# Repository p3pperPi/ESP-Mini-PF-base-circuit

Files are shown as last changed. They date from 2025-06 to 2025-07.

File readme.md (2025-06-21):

# 概要
ESP32を使用して、DCブラシモータを使用したライントレースをするための基板です。

# 回路図

回路図

# 機能
## 電源
J1の PHコネクタ、もしくは J3の XT60コネクタに電源を接続してください。
J1の PHコネクタを使用する際は、J2の PHコネクタにスイッチをつないでください。

入力可能な電圧の範囲はは ** 30V** です。

また、JP17をショートすることで、モータ電源にUSB 5Vを使用することが可能です。
ただし、JP17をショートした状態で電源コネクタに5V以外の電圧をかけると、接続した機器が破損します。
**JP17をショートさせた際は、絶対に電源コネクタから給電は行わないでください。**
なお、JP17にはダイオードを入れて逆流防止を行うことも可能です。その際は、[SBM245L](https://akizukidenshi.com/catalog/g/g117439/)を使用してください。

入力電源は、DCDCコンバータモジュール[CN39033A](https://japanese.alibaba.com/product-detail/CN3903-3A-Mini-Buck-Step-Down-1600380707339.html)を使用して5Vまで電圧を下げられます。

| 項目 | 値  | 単位 |
| --- | --- | ---- |
| 最大定格入力電圧 | 30  | V |
| 出力電流(Max.) | 3 | A |

上で生成された5Vから、[UZ1085L-22-TN3-R](https://www.lcsc.com/product-detail/Low-Dropout-Regulators-LDO_UZ1085L-AD-TN3-R_C146666.html)を使用し、マイコンへの電源供給を行います。
| 項目 | 値  | 単位 |
| --- | --- | ---- |
| 最大定格入力電圧 | 18  | V |
| 最大電流(Typ.) | 4 | A |

## マイコン
ESP32-WROOM-32を使用します。  
[CH340X](https://www.lcsc.com/product-detail/USB-Converters_WCH-Jiangsu-Qin-Heng-CH340X_C3035748.html?s_z=n_CH340X)を使用した書き込み回路を持ちます。

## DCブラシモータ
モータドライバIC[CP3119MDTR](https://www.lcsc.com/product-detail/Brushed-DC-Motor-Drivers_XBLW-CP3119MDTR-XBLW_C42395499.html)を使用して、DCモータを制御します。

| 項目 | 値 | 単位 |
| --- | --- | --- |
| 最大定格電圧 | 32 | V |
| 最大定格電流 | 8.0 | A |
| 推奨電源電圧範囲 | 3.0~30.0 | V |
| 推奨最大電流 | 6.0 | A |
| FETオン抵抗 (load=1A) | 80 | m $\Omega$ |
| FETオン抵抗 (load=3A) | 110 | m $\Omega$ |

## エンコーダ
A/B相のシングルエンドエンコーダをカウントします。エンコーダの電源電圧と信号入力は5Vです。
[TXB0104RUT](https://lcsc.com/product-detail/translators-level-shifters_texas-instruments-txb0104rutr_C105266.html)により、5V信号を3.3Vに変換してESP32に信号を入力します。
パルス入力ピンは、ソルダジャンパ(JP2 ~ 5)によりプルアップが可能です。
プルアップの有無については、[ジャンパの機能](#ジャンパの機能)を参照してください。

## 汎用IO
サーボモータ、センサ入力等のための、汎用のIOです。
ピンアサインは下記の通りです。

| ピン | 機能 |
| ---- | --- |
| 1 | IOピン |
| 2 | Vs |
| 3 | GND |

ピン番号は、[ピンアサイン](#ピンアサイン)を参照してください。

Vsは、ソルダジャンパ(JP6 ~ 9)により電圧を選択可能です。
選択される電圧は、[ジャンパの機能](#ジャンパの機能)を参照してください。

## フォトリフレクタ
[ITR8307/S17/TR8(B)](https://www.lcsc.com/product-detail/Reflective-Optical-Interrupters_Everlight-Elec-ITR8307-S17-TR8-B_C81632.html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) を3つ搭載し、テープの判定を行います。

また、外付けのLED・フォトトランジスタを使用することも可能です。いずれも外形3mmの砲弾型のものを使用してください。

使用するフォトリフレクタの選択は、JP10～JP15 を使用してください。

## LED
3mm砲弾型LEDを4つ搭載可能です。  
D2は、電源投入時に点灯します。  
D3, D4, D5はESP32から点灯/消灯 を管理可能です。

# ピンアサイン

ESP32-WROOM-32のピンアサインは下記の通りです。

| ピン | IO pin | 機能 | IN/OUT |
| ---- | --- | --- | --- |
| 27 | IO16 | モータL出力1 | OUT (PWM) |
| 28 | IO17 | モータL出力2 | OUT (PWM) |
| 30 | IO18 | モータR出力1 | OUT (PWM) |
| 31 | IO19 | モータR出力2 | OUT (PWM) |
| 16 | IO13 | エンコーダL入力1 | IN (PWM) |
| 13 | IO14 | エンコーダL入力2 | IN (PWM) |
| 10 | IO25 | エンコーダR入力1 | IN (PWM) |
| 11 | IO26 | エンコーダR入力2 | IN (PWM) |
| 34 | IO3/RxD0 | PCとのUART RxD | IN (COM.) |
| 35 | IO1/TxD0 | PCとのUART TxD | OUT (COM.) |
| 25 | IO0 | Boot | - |
| 9 | IO33 | ラインセンサ1 | IN(Analog) |
| 6 | IO34 | ラインセンサ2 | IN(Analog) |
| 8 | IO35 | ラインセンサ3 | IN(Analog) |
| 33 | IO21 | LED 赤 | OUT(Digital) |
| 36 | IO22 | LED 黄 | OUT(Digital) |
| 37 | IO23 | LED 緑 | OUT(Digital) |
| 8 | IO32 | 汎用IO 0 | IN/OUT |
| 12 | IO27 | 汎用IO 1 | IN/OUT |
| 26 | IO4 | 汎用IO 2 | IN/OUT |
| 29 | IO5 | 汎用IO 3(プルアップ) | IN/OUT |
| 4 | IO36(SENSOR_VP) | 電源電圧監視(1/10) | IN(Analog) |

# ジャンパの機能

ジャンパにより、機能を切り替えることができます。

| ジャンパ | 機能 | モード1  | 機能1 | モード2  | 機能2 | デフォルト | 備考 |
| --- | --- | --- | --- | --- | --- | --- | --- |
| JP1 | Power_SW_Disable | オープン | J2 パワースイッチが有効 | ショート | J2 パワースイッチが無効(常時ショート) | オープン | - |
| JP2 | L1_PU | オープン | エンコーダL1の入力は電圧入力 | ショート | エンコーダL1の入力をプルアップ(1k) | オープン | - |
| JP3 | L2_PU | オープン | エンコーダL2の入力は電圧入力 | ショート | エンコーダL2の入力をプルアップ(1k) | オープン | - |
| JP4 | R1_PU | オープン | エンコーダR1の入力は電圧入力 | ショート | エンコーダR1の入力をプルアップ(1k) | オープン | - |
| JP5 | R2_PU | オープン | エンコーダR2の入力は電圧入力 | ショート | エンコーダR2の入力をプルアップ(1k) | オープン | - |
| JP6 | Vs_SEL0 | 3.3 | 汎用入力J9 の2番ピンを3.3Vにする | Vin | 汎用入力J9 の2番ピンをVinにする | オープン | オープンだと2番ピンはNC |
| JP7 | Vs_SEL1 | 3.3 | 汎用入力J10 の2番ピンを3.3Vにする | Vin | 汎用入力J10 の2番ピンをVinにする | オープン | オープンだと2番ピンはNC |
| JP8 | Vs_SEL2 | 3.3 | 汎用入力J11 の2番ピンを3.3Vにする | Vin | 汎用入力J11 の2番ピンをVinにする | オープン | オープンだと2番ピンはNC |
| JP9 | Vs_SEL3 | 3.3 | 汎用入力J12 の2番ピンを3.3Vにする | Vin | 汎用入力J12 の2番ピンをVinにする | オープン | オープンだと2番ピンはNC |
| JP10 | LED_SEL1 | SMD | ラインセンサ(U8)の LEDを有効化 | DIP | D6 のLEDを有効化 | オープン | オープンだとU8, D6いずれのLEDも光らない  |
| JP11 | PT_SEL1 | SMD | SENSOR1 の入力をラインセンサU8 にする  | DIP | SENSOR1 の入力をQ1 にする | オープン | オープンだとSENSOR1 はN.C. |
| JP12 | LED_SEL2 | SMD | ラインセンサ(U9)の LEDを有効化 | DIP | D7 のLEDを有効化 | オープン | オープンだとU9, D7いずれのLEDも光らない  |
| JP13 | PT_SEL2 | SMD | SENSOR2 の入力をラインセンサU9 にする  | DIP | SENSOR2 の入力をQ2 にする | オープン | オープンだとSENSOR2 はN.C. |
| JP14 | LED_SEL2 | SMD | ラインセンサ(U10)の LEDを有効化 | DIP | D8 のLEDを有効化 | オープン | オープンだとU10, D8いずれのLEDも光らない |
| JP15 | PT_SEL2 | SMD | SENSOR3 の入力をラインセンサU10 にする | DIP | SENSOR3 の入力をQ1 にする | オープン | オープンだとSENSOR3 はN.C. |
| JP16 | Reseet | オープン | 通常動作 | ショート | リセット | オープン | スイッチ取付可 |
| JP17 | USB＿Vs | オープン | 外部電源をモータ電源とする | ショート | USB電源をモータ電源とする | オープン | ショートの代わりにダイオードを使用可 |

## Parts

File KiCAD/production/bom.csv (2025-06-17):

Designator | Footprint | Quantity | Value | LCSC Part #
C1, C2 | CP_Radial_D5.0mm_P2.00mm | 2 | 22u | x
C10, C3, C4, C8 | 0402 | 4 | 0.1u | C77020
C5 | 0402 | 1 | 10u | C76991
C6 | 0402 | 1 | 20p | C76959
C7, C9 | CP_Radial_D8.0mm_P3.50mm | 2 | 470u | x
D1 | D_SMA | 1 | CDBA240LL-HF | C2886093
D2 | LED_D3.0mm | 1 | LED_POWER | x
D3 | LED_D3.0mm | 1 | LED_R | x
D4 | LED_D3.0mm | 1 | LED_Y | x
D5 | LED_D3.0mm | 1 | LED_G | x
D6, D7, D8 | LED_D3.0mm | 3 | U4_ALT1 | x
F1 | 0603 | 1 | BSMD0603-050-6V | C883095
J1 | JST_PH_B2B-PH-K_1x02_P2.00mm_Vertical | 1 | Vin_1 | x
J10 | PinHeader_1x03_P2.54mm_Vertical | 1 | IO27_GPIO1 | x
J11 | PinHeader_1x03_P2.54mm_Vertical | 1 | IO32_GPIO2 | x
J12 | PinHeader_1x03_P2.54mm_Vertical | 1 | IO5_GPIO3(PU) | x
J2 | JST_PH_B2B-PH-K_1x02_P2.00mm_Vertical | 1 | Power_SW | x
J3 | AMASS_XT60-M_1x02_P7.20mm_Vertical | 1 | Vin_XT | x
J4 | USB_Micro-B_Amphenol_10103594-0001LF_Horizontal | 1 | USB_B_Micro | C428495
J5 | JST_ZH_B4B-ZH-A_1x04_P1.50mm_Vertical | 1 | Encorder_L | x
J6 | JST_ZH_B4B-ZH-A_1x04_P1.50mm_Vertical | 1 | Encorder_R | x
J7 | TerminalBlock_bornier-2_P5.08mm | 1 | MOTOR_L | x
J8 | TerminalBlock_bornier-2_P5.08mm | 1 | MOTOR_R | x
J9 | PinHeader_1x03_P2.54mm_Vertical | 1 | IO4_GPIO0 | x
JP1 | SolderJumper-2_P1.3mm_Open_RoundedPad1.0x1.5mm | 1 | Power_SW_DIisable | x
JP10, JP12, JP14 | SolderJumper-3_P1.3mm_Open_RoundedPad1.0x1.5mm | 3 | LED_SEL1 | x
JP11, JP13, JP15 | SolderJumper-3_P1.3mm_Open_RoundedPad1.0x1.5mm | 3 | PT_SEL1 | x
JP16 | SolderJumper-2_TVAF06-A020B-R_COMPATIBLE | 1 | Reset | x
JP17 | D_DO-41_SOD81_P7.62mm_Horizontal | 1 | USB_Vs | x
JP2 | SolderJumper-2_P1.3mm_Open_RoundedPad1.0x1.5mm | 1 | L1_PU | x
JP3 | SolderJumper-2_P1.3mm_Open_RoundedPad1.0x1.5mm | 1 | L2_PU | x
JP4 | SolderJumper-2_P1.3mm_Open_RoundedPad1.0x1.5mm | 1 | R1_PU | x
JP5 | SolderJumper-2_P1.3mm_Open_RoundedPad1.0x1.5mm | 1 | R2_PU | x
JP6 | SolderJumper-3_P1.3mm_Open_RoundedPad1.0x1.5mm | 1 | Vs_SEL0 | x
JP7 | SolderJumper-3_P1.3mm_Open_RoundedPad1.0x1.5mm | 1 | Vs_SEL1 | x
JP8 | SolderJumper-3_P1.3mm_Open_RoundedPad1.0x1.5mm | 1 | Vs_SEL2 | x
JP9 | SolderJumper-3_P1.3mm_Open_RoundedPad1.0x1.5mm | 1 | Vs_SEL3 | x
Q1, Q2, Q3 | LED_D3.0mm | 3 | U4_ALT2 | x
R1 | 0402 | 1 | 18k | C316875
R10, R11, R12, R13, R17, R18, R19, R20, R22, R24, R26, R6, R8 | 0402 | 13 | 1k | C159872
R14, R15, R16, R7, R9 | 0402 | 5 | 560 | C427239
R2 | 0402 | 1 | 2k | C173345
R21, R23, R25 | 0805 | 3 | 50 | C2828866
R3, R4 | 0402 | 2 | 22 | C400511
R5 | 0402 | 1 | 4.7k | C159885
U1 | DCDC_Conv_CN39033A | 1 | CN39033A | x
U10, U8, U9 | Everlight_ITR1201SR10AR | 3 | ITR8307-S17-TR8 | C81632
U2 | MSOP-10_3x3mm_P0.5mm | 1 | CH340X | C3035748
U3 | TO-252-2 | 1 | UZ1085L-33-TN3-R | C125622
U4 | Texas_R-PUQFN-N12 | 1 | TXB0104RUT | C105266
U5, U6 | SOP-8_3.9x4.9mm_P1.27mm | 2 | CP3119MDTR | C42395499
U7 | ESP32-WROOM-32_39P-TH | 1 | ESP32-WROOM-32 | x

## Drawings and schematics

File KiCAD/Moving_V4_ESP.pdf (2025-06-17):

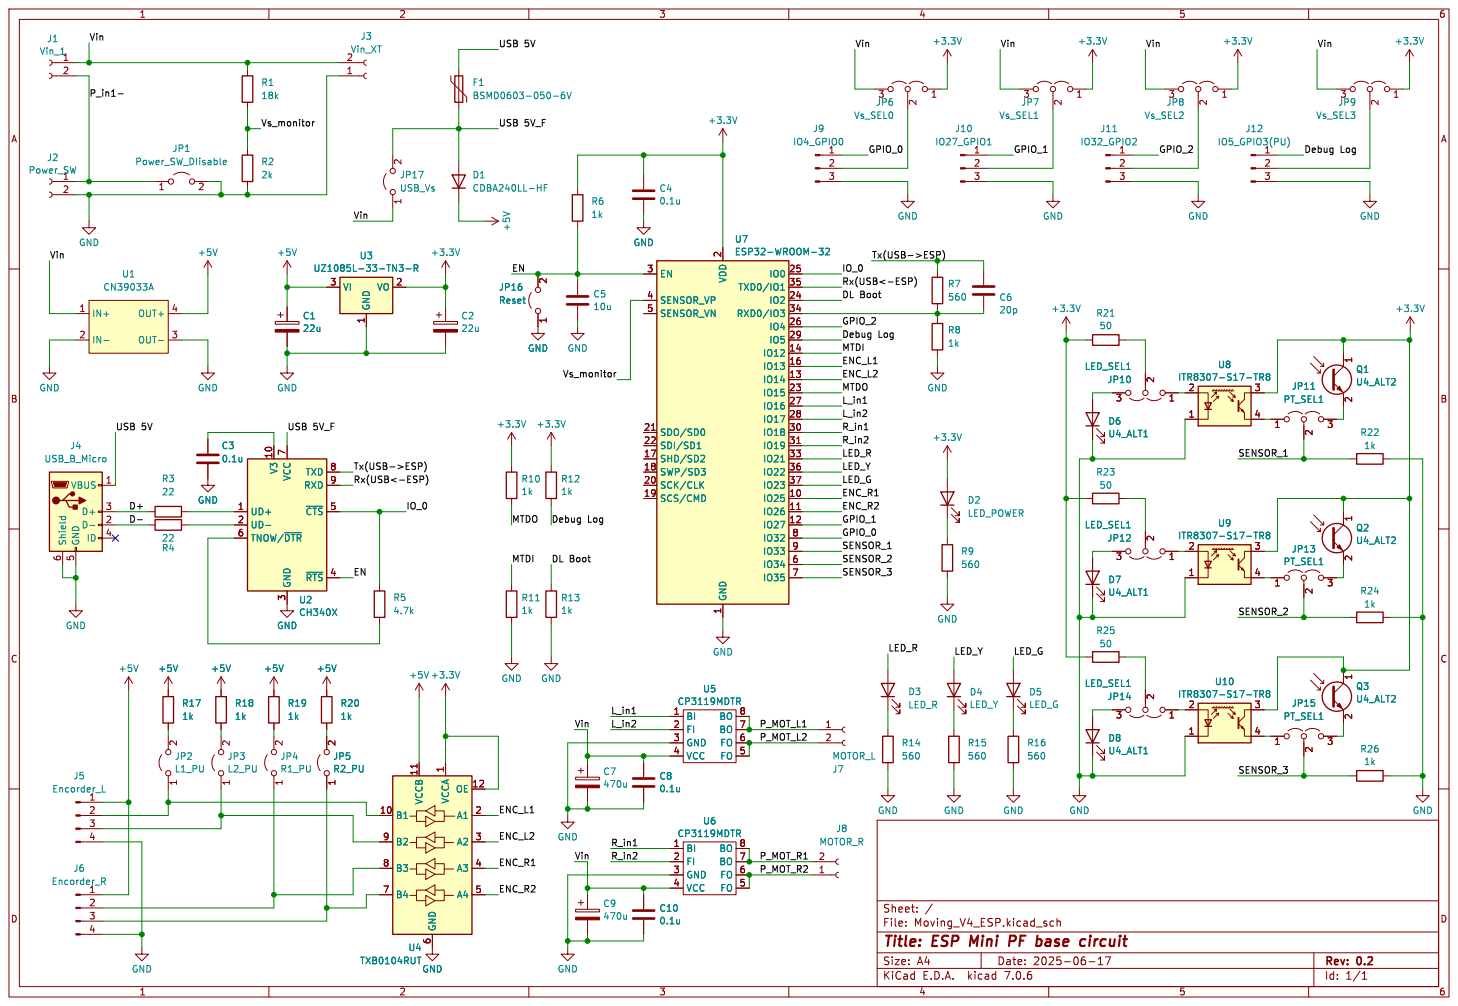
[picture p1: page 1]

2 SCK/CLK 20 SDO/SD0 21 SDI/SD1 22

7 TXD 8 RXD 9 U2 CH340X GND GND

3 ~{RTS}4 ~{CTS}5 TNOW/~{DTR} 6 VCC

Tx(USB->ESP) EN
IO_0 Rx(USB<-ESP)

Id: 1/1 Title: ESP Mini PF base circuit File: Moving_V4_ESP.kicad_sch Sheet: / +5V

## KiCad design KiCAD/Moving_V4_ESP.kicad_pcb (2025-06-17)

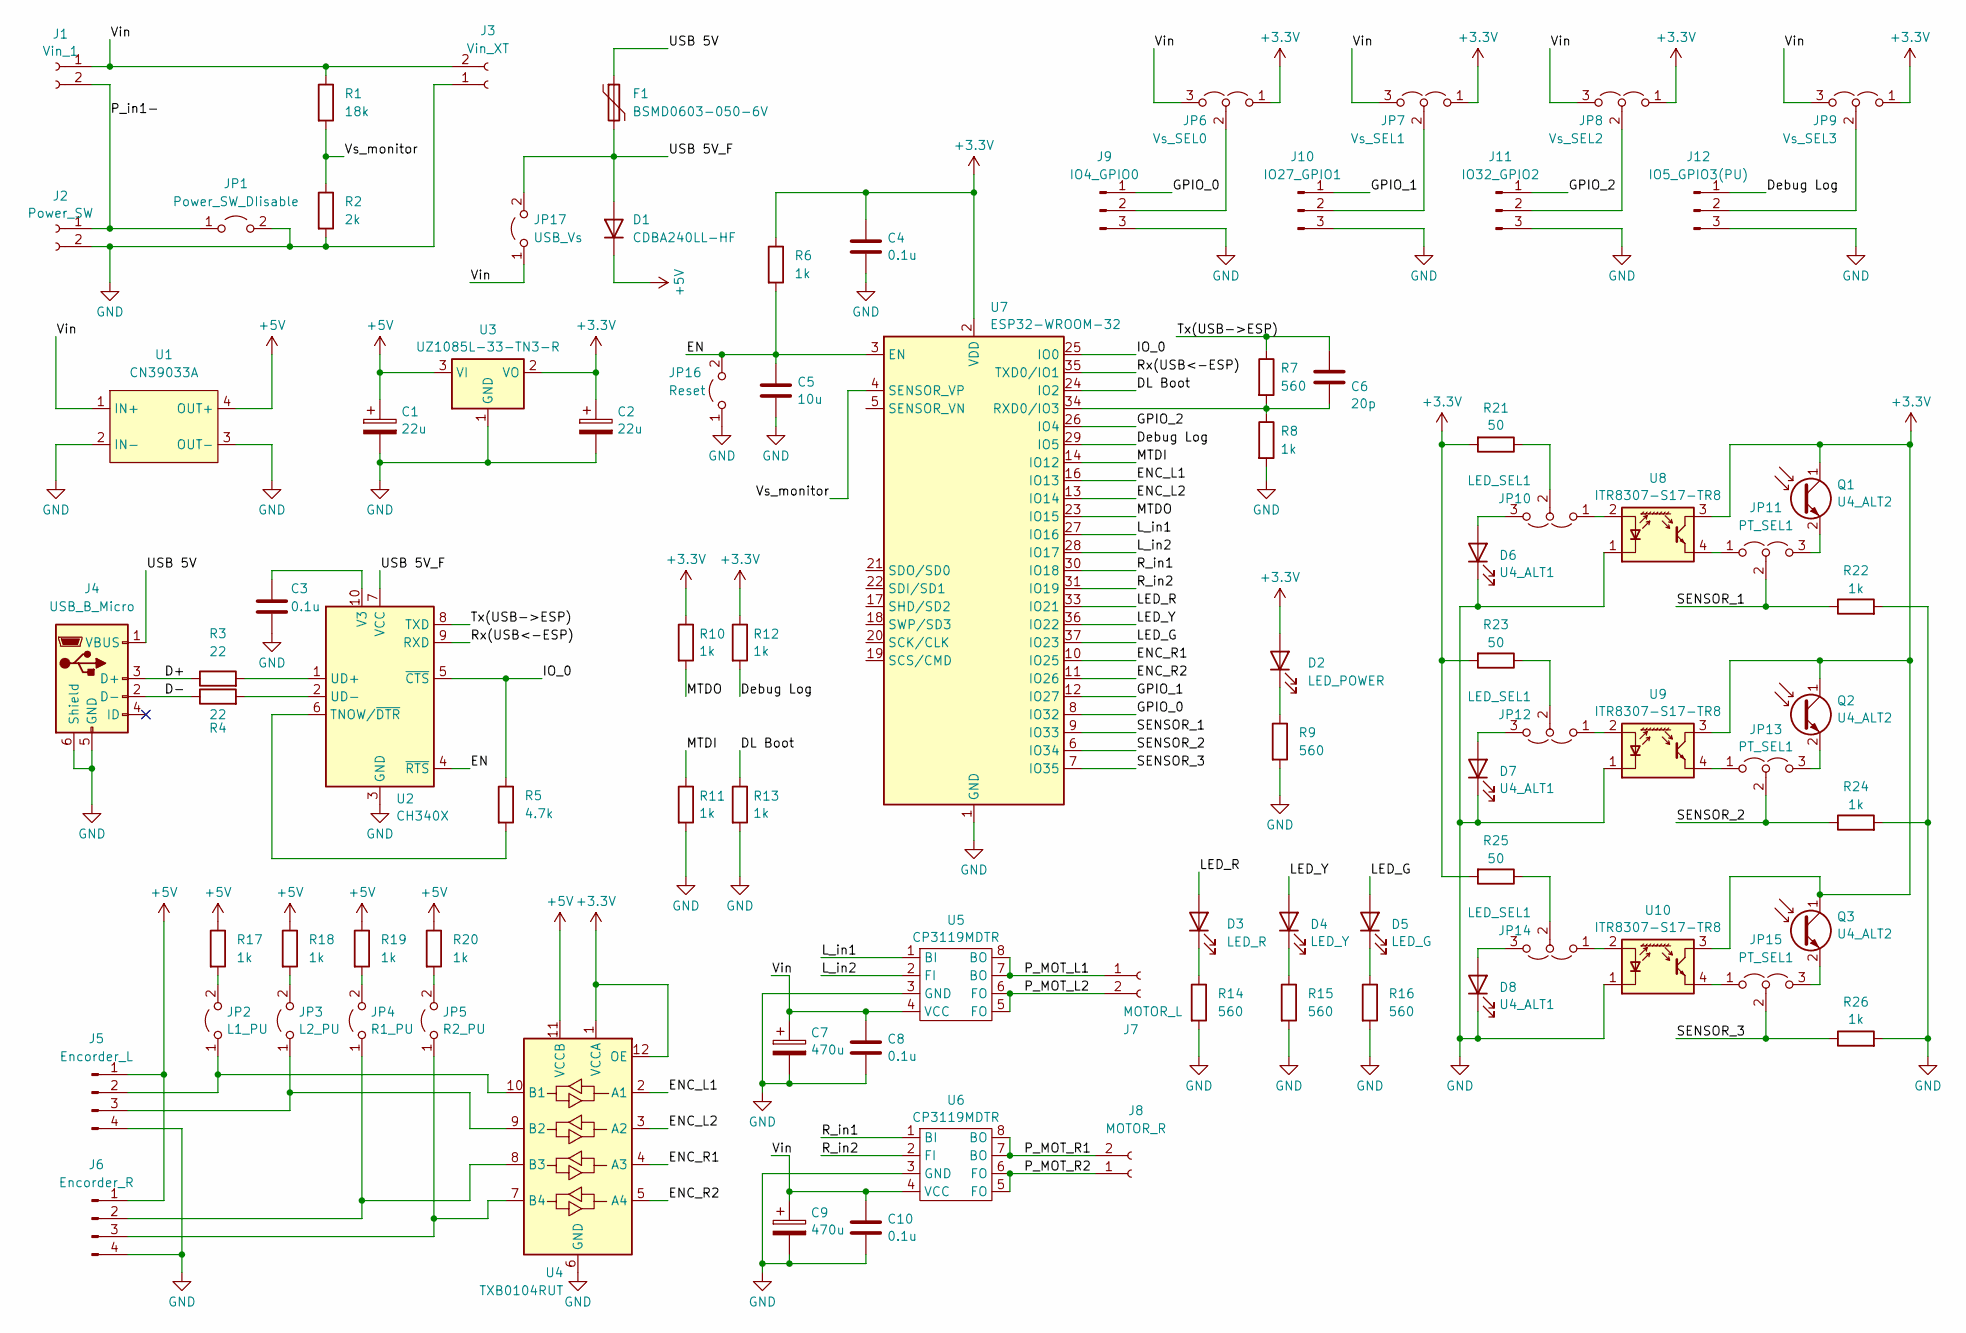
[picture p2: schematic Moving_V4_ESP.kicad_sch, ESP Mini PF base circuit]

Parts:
C1, C2: 22u; CP_Radial_D5.0mm_P2.00mm; LCSC x
C3, C4, C8, C10: 0.1u; C_0402_1005Metric; LCSC C77020
C5: 10u; C_0402_1005Metric; LCSC C76991
C6: 20p; C_0402_1005Metric; LCSC C76959
C7, C9: 470u; CP_Radial_D8.0mm_P3.50mm; LCSC x
D1: CDBA240LL-HF; D_SMA; LCSC C2886093
D2: LED_POWER; LED_D3.0mm; LCSC x
D3: LED_R; LED_D3.0mm; LCSC x
D4: LED_Y; LED_D3.0mm; LCSC x
D5: LED_G; LED_D3.0mm; LCSC x
D6, D7, D8: U4_ALT1; LED_D3.0mm; LCSC x
F1: BSMD0603-050-6V; Fuse_0603_1608Metric; LCSC C883095
J1: Vin_1; JST_PH_B2B-PH-K_1x02_P2.00mm_Vertical; LCSC x
J2: Power_SW; JST_PH_B2B-PH-K_1x02_P2.00mm_Vertical; LCSC x
J3: Vin_XT; AMASS_XT60-M_1x02_P7.20mm_Vertical; LCSC x
J4: USB_B_Micro; USB_Micro-B_Amphenol_10103594-0001LF_Horizontal; LCSC C428495
J5: Encorder_L; JST_ZH_B4B-ZH-A_1x04_P1.50mm_Vertical; LCSC x
J6: Encorder_R; JST_ZH_B4B-ZH-A_1x04_P1.50mm_Vertical; LCSC x
J7: MOTOR_L; TerminalBlock_bornier-2_P5.08mm; LCSC x
J8: MOTOR_R; TerminalBlock_bornier-2_P5.08mm; LCSC x
J9: IO4_GPIO0; PinHeader_1x03_P2.54mm_Vertical; LCSC x
J10: IO27_GPIO1; PinHeader_1x03_P2.54mm_Vertical; LCSC x
J11: IO32_GPIO2; PinHeader_1x03_P2.54mm_Vertical; LCSC x
J12: IO5_GPIO3(PU); PinHeader_1x03_P2.54mm_Vertical; LCSC x
JP1: Power_SW_DIisable; SolderJumper-2_P1.3mm_Open_RoundedPad1.0x1.5mm; LCSC x
JP2: L1_PU; SolderJumper-2_P1.3mm_Open_RoundedPad1.0x1.5mm; LCSC x
JP3: L2_PU; SolderJumper-2_P1.3mm_Open_RoundedPad1.0x1.5mm; LCSC x
JP4: R1_PU; SolderJumper-2_P1.3mm_Open_RoundedPad1.0x1.5mm; LCSC x
JP5: R2_PU; SolderJumper-2_P1.3mm_Open_RoundedPad1.0x1.5mm; LCSC x
JP6: Vs_SEL0; SolderJumper-3_P1.3mm_Open_RoundedPad1.0x1.5mm; LCSC x
JP7: Vs_SEL1; SolderJumper-3_P1.3mm_Open_RoundedPad1.0x1.5mm; LCSC x
JP8: Vs_SEL2; SolderJumper-3_P1.3mm_Open_RoundedPad1.0x1.5mm; LCSC x
JP9: Vs_SEL3; SolderJumper-3_P1.3mm_Open_RoundedPad1.0x1.5mm; LCSC x
JP10, JP12, JP14: LED_SEL1; SolderJumper-3_P1.3mm_Open_RoundedPad1.0x1.5mm; LCSC x
JP11, JP13, JP15: PT_SEL1; SolderJumper-3_P1.3mm_Open_RoundedPad1.0x1.5mm; LCSC x
JP16: Reset; SolderJumper-2_TVAF06-A020B-R_COMPATIBLE; LCSC x
JP17: USB_Vs; D_DO-41_SOD81_P7.62mm_Horizontal; LCSC x
Q1, Q2, Q3: U4_ALT2; LED_D3.0mm; LCSC x
R1: 18k; R_0402_1005Metric; LCSC C316875
R2: 2k; R_0402_1005Metric; LCSC C173345
R3, R4: 22; R_0402_1005Metric; LCSC C400511
R5: 4.7k; R_0402_1005Metric; LCSC C159885
R6, R8, R10, R11, R12, R13, R17, R18, R19, R20, R22, R24, R26: 1k; R_0402_1005Metric; LCSC C159872
R7, R9, R14, R15, R16: 560; R_0402_1005Metric; LCSC C427239
R21, R23, R25: 50; R_0805_2012Metric; LCSC C2828866
U1: CN39033A; DCDC_Conv_CN39033A; LCSC x
U2: CH340X; MSOP-10_3x3mm_P0.5mm; LCSC C3035748
U3: UZ1085L-33-TN3-R; TO-252-2; LCSC C125622
U4: TXB0104RUT; Texas_R-PUQFN-N12; LCSC C105266
U5, U6: CP3119MDTR; SOP-8_3.9x4.9mm_P1.27mm; LCSC C42395499
U7: ESP32-WROOM-32; ESP32-WROOM-32_39P-TH; LCSC x
U8, U9, U10: ITR8307-S17-TR8; Everlight_ITR1201SR10AR; LCSC C81632

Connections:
+3.3V: C2.1, C4.1, D2.2 (A), JP6.1 (A), JP7.1 (A), JP8.1 (A), JP9.1 (A), Q1.1 (C), Q2.1 (C), Q3.1 (C), R6.1, R10.1, R12.1, R21.2, R23.2, R25.2, U3.2 (VO), U4.1 (VCCA), U4.12 (OE), U7.2 (VDD), U8.3, U9.3, U10.3
+5V: C1.1, D1.1 (K), J5.1, J6.1, R17.1, R18.1, R19.1, R20.1, U1.4 (OUT+), U3.3 (VI), U4.11 (VCCB)
/D+: J4.3 (D+), R3.1
/D-: J4.2 (D-), R4.1
/DL Boot: R13.1, U7.24 (IO2)
/Debug Log: J12.1, R12.2, U7.29 (IO5)
/EN: C5.1, JP16.2 (B), R6.2, U2.4 (~RTS), U7.3 (EN)
/ENC_L1: U4.2 (A1), U7.16 (IO13)
/ENC_L2: U4.3 (A2), U7.13 (IO14)
/ENC_R1: U4.4 (A3), U7.10 (IO25)
/ENC_R2: U4.5 (A4), U7.11 (IO26)
/GPIO_0: J9.1, U7.8 (IO32)
/GPIO_1: J10.1, U7.12 (IO27)
/GPIO_2: J11.1, U7.26 (IO4)
/IO_0: R5.1, U2.5 (~CTS), U7.25 (IO0)
/LED_G: D5.2 (A), U7.37 (IO23)
/LED_R: D3.2 (A), U7.33 (IO21)
/LED_Y: D4.2 (A), U7.36 (IO22)
/L_in1: U5.1 (BI), U7.27 (IO16)
/L_in2: U5.2 (FI), U7.28 (IO17)
/MTDI: R11.1, U7.14 (IO12)
/MTDO: R10.2, U7.23 (IO15)
/P_MOT_L1: J7.1, U5.7 (BO), U5.8 (BO)
/P_MOT_L2: J7.2, U5.5 (FO), U5.6 (FO)
/P_MOT_R1: J8.2, U6.7 (BO), U6.8 (BO)
/P_MOT_R2: J8.1, U6.5 (FO), U6.6 (FO)
/P_in1-: J1.2, J2.1, JP1.1 (A)
/R_in1: U6.1 (BI), U7.30 (IO18)
/R_in2: U6.2 (FI), U7.31 (IO19)
/Rx(USB<-ESP): U2.9 (RXD), U7.35 (TXD0/IO1)
/SENSOR_1: JP11.2 (C), R22.1, U7.9 (IO33)
/SENSOR_2: JP13.2 (C), R24.1, U7.6 (IO34)
/SENSOR_3: JP15.2 (C), R26.1, U7.7 (IO35)
/Tx(USB->ESP): C6.1, R7.1, U2.8 (TXD)
/USB 5V: F1.1, J4.1 (VBUS)
/USB 5V_F: D1.2 (A), F1.2, JP17.2 (B), U2.7 (VCC)
/Vin: C7.1, C8.1, C9.1, C10.1, J1.1, J3.2, JP6.3 (B), JP7.3 (B), JP8.3 (B), JP9.3 (B), JP17.1 (A), R1.1, U1.1 (IN+), U5.4 (VCC), U6.4 (VCC)
/Vs_monitor: R1.2, R2.1, U7.4 (SENSOR_VP)
GND: C1.2, C2.2, C3.2, C4.2, C5.2, C7.2, C8.2, C9.2, C10.2, D6.1 (K), D7.1 (K), D8.1 (K), J2.2, J3.1, J4.5 (GND), J4.6 (Shield), J5.4, J6.4, J9.3, J10.3, J11.3, J12.3, JP1.2 (B), JP16.1 (A), R2.2, R8.2, R9.2, R11.2, R13.2, R14.2, R15.2, R16.2, R22.2, R24.2, R26.2, U1.2 (IN-), U1.3 (OUT-), U2.3 (GND), U3.1 (GND), U4.6 (GND), U5.3 (GND), U6.3 (GND), U7.1 (GND), U7.15 (GND), U7.38 (GND), U7.39 (GND), U8.1 (K), U9.1 (K), U10.1 (K)
unnamed: D2.1 (K), R9.1
unnamed: D3.1 (K), R14.1
unnamed: D4.1 (K), R15.1
unnamed: D5.1 (K), R16.1
unnamed: D6.2 (A), JP10.3 (B)
unnamed: D7.2 (A), JP12.3 (B)
unnamed: D8.2 (A), JP14.3 (B)
unnamed: J5.2, JP2.1 (A), U4.10 (B1)
unnamed: J5.3, JP3.1 (A), U4.9 (B2)
unnamed: J6.2, JP4.1 (A), U4.8 (B3)
unnamed: J6.3, JP5.1 (A), U4.7 (B4)
unnamed: J9.2, JP6.2 (C)
unnamed: J10.2, JP7.2 (C)
unnamed: J11.2, JP8.2 (C)
unnamed: J12.2, JP9.2 (C)
unnamed: JP2.2 (B), R17.2
unnamed: JP3.2 (B), R18.2
unnamed: JP4.2 (B), R19.2
unnamed: JP5.2 (B), R20.2
unnamed: JP10.1 (A), U8.2 (A)
unnamed: JP10.2 (C), R21.1
unnamed: JP11.1 (A), U8.4
unnamed: JP11.3 (B), Q1.2 (E)
unnamed: JP12.1 (A), U9.2 (A)
unnamed: JP12.2 (C), R23.1
unnamed: JP13.1 (A), U9.4
unnamed: JP13.3 (B), Q2.2 (E)
unnamed: JP14.1 (A), U10.2 (A)
unnamed: JP14.2 (C), R25.1
unnamed: JP15.1 (A), U10.4
unnamed: JP15.3 (B), Q3.2 (E)
unnamed: R5.2, U2.6 (TNOW/~DTR)
unnamed: R3.2, U2.1 (UD+)
unnamed: R4.2, U2.2 (UD-)
unnamed: C3.1, U2.10 (V3)
unnamed: C6.2, R7.2, R8.1, U7.34 (RXD0/IO3)

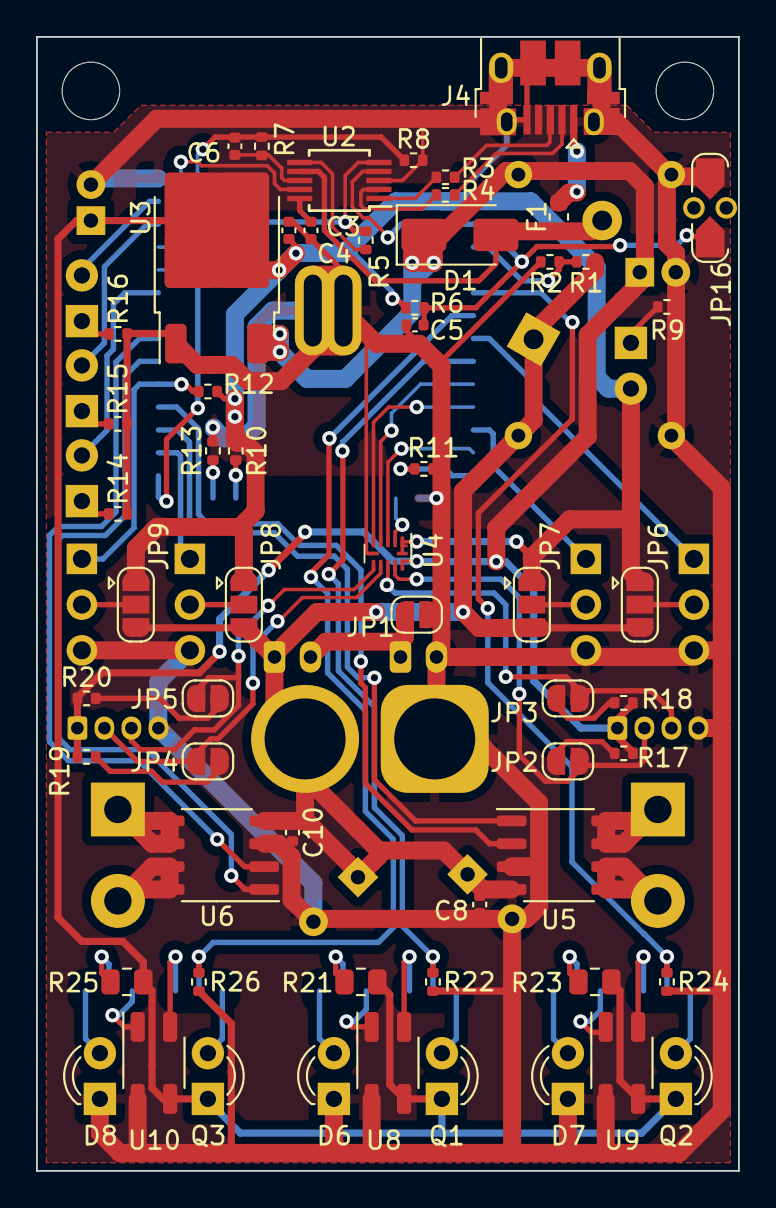
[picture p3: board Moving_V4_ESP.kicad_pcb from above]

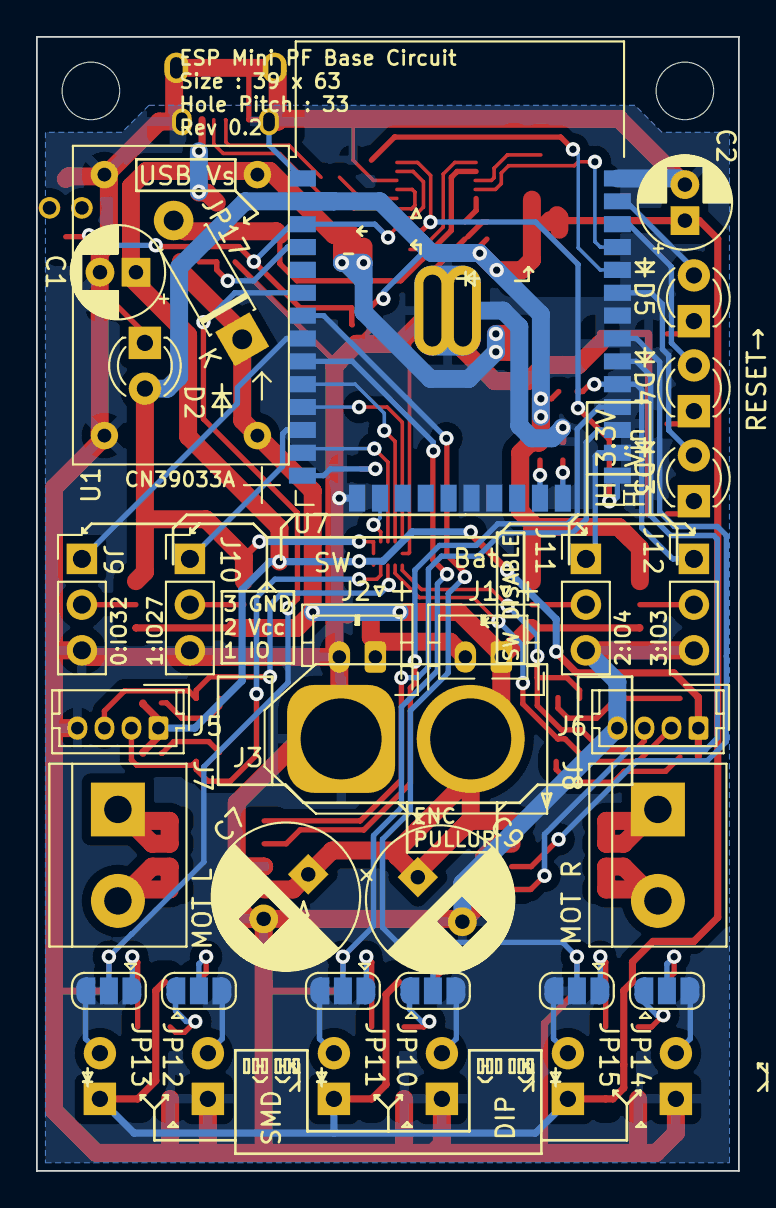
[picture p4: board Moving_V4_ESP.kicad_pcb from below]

Board: 2 copper layers, 39.0 x 63.0 mm, 87 parts (28 on the bottom side), 75 nets.

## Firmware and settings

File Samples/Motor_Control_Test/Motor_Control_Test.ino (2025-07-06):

#include "../mini_PF_pins.hpp"
#include "driver/pcnt.h"

// pcnt : ESP32 の パルスカウンタ
// ライブラリの詳細：
// https://github.com/m5stack/azure_iothub_arduino_lib_esp32/blob/master/hardware/espressif/esp32/tools/sdk/include/driver/driver/pcnt.h
// https://docs.espressif.com/projects/esp-idf/en/v5.4.1/esp32/api-reference/peripherals/pcnt.html

// タイマ割り込み：Arduino-ESP32 の TImer
// 機能の詳細
// https://docs.espressif.com/projects/arduino-esp32/en/latest/api/timer.html

// エンコーダ周りの定義

// 速度を移動平均するための設定
#define SPEED_BUFFER_LENGTH 5
const int  SPEED_AVE_WEIGHT[SPEED_BUFFER_LENGTH] = {6, 5, 2, 2, 1}; // 重み付けの設定、総和がビットシフトで演算できる値にする
const int  SPEED_AVE_DIVISOR = 16; // 重みの総和

volatile  int64_t pulse_R[SPEED_BUFFER_LENGTH];
volatile  int64_t pulse_L[SPEED_BUFFER_LENGTH];
volatile  int32_t pulse_diff_R[SPEED_BUFFER_LENGTH];
volatile  int32_t pulse_diff_L[SPEED_BUFFER_LENGTH];
volatile  int32_t crnt_pulse_per_sec_R = 0;
volatile  int32_t crnt_pulse_per_sec_L = 0;
volatile uint16_t pulse_itr = 0;



volatile uint32_t time_diff = 0xFFFFFFFF;// 意図しない0割りを防ぐため大きな値を初期値とする
volatile uint64_t last_read_time = 0;


// 速度制御周り
volatile  int32_t tgt_pulse_per_sec_R = 0;
volatile  int32_t tgt_pulse_per_sec_L = 0;
volatile  int32_t out_L = 0;
volatile  int32_t out_R = 0;

const     int32_t OUTTPUT_LIMIT_UPPER =  255; //出力の上限
const     int32_t OUTTPUT_LIMIT_LOWER = -255; //出力の下限

const     int32_t INTEGRAL_LIMIT = 0xFFFFF;
const     int32_t DEFAULT_CONTROL_TIMESPAN = 10; // 制御周期のデフォルト値（ミリ秒）
const     int32_t OUTPUT_SCALE_MULTIPLIER =    1; // 出力のスケール倍率
const     int32_t OUTPUT_SCALE_DIVISOR    = 1000; // 出力のスケール除数
// 出力スケールについて：
// 入力値：パルス/マイクロ秒：～2000 程度
// 出力値：-255 ～ 255
// 入力値と出力値のオーダーを合わさるための係数

int32_t integral_L = 0;
int32_t integral_R = 0;
int32_t error_L = 0;
int32_t error_R = 0;
int32_t prev_error_L = 0;
int32_t prev_error_R = 0;

int32_t Speed_Kp =  80;
int32_t Speed_Ki =   1;
int32_t Speed_Kd =   0;




// カウンタオーバーフロー処理
#define COUNTER_SKIP_THRESHOLD    3000
#define COUNTER_MAX               5000
#define COUNTER_MIN              -5000

int16_t cnt_crnt[8] = {0, 0, 0, 0, 0, 0, 0, 0}; 
int16_t cnt_prv [8] = {0, 0, 0, 0, 0, 0, 0, 0}; 

int32_t getDiff(pcnt_unit_t unit,byte cnt_no = 0){
    // カウンタの値を読み取る
    pcnt_get_counter_value(unit, &cnt_crnt[cnt_no]);
    int32_t cnt_diff = cnt_crnt[cnt_no] - cnt_prv[cnt_no];
    cnt_prv[cnt_no] = cnt_crnt[cnt_no];

    // オーバーフローの処理
    // カウンタはオーバーフローすると0に戻る
    if (cnt_diff < -COUNTER_SKIP_THRESHOLD) {
        // カウンタが最大値から0に戻った場合
        cnt_diff += COUNTER_MAX;
    } else if (cnt_diff > COUNTER_SKIP_THRESHOLD) {
        // カウンタが最小値から0に戻った場合
        cnt_diff += COUNTER_MIN;
    }

    return cnt_diff;
}


// タイマ割り込み周りの定義
// エンコーダ速度計測
#define SPEED_CONTROL_TIMER_FREQ  100000
#define SPEED_CONTROL_TIMER_COUNT   1000

hw_timer_t * speed_control_timer = NULL;
volatile SemaphoreHandle_t speed_control_timer_semaphore;
portMUX_TYPE speed_control_timer_mux = portMUX_INITIALIZER_UNLOCKED;


// 速度制御用のタイマ割り込みハンドラ
void ARDUINO_ISR_ATTR speedTimerInterrupt(){
    portENTER_CRITICAL_ISR(&speed_control_timer_mux);

    // バッファイテレータのインクリメント
    pulse_itr = (pulse_itr + 1) % SPEED_BUFFER_LENGTH;

    //  カウンタの値取得
    time_diff = millis() - last_read_time;
    last_read_time += time_diff;
    pulse_diff_L[pulse_itr] = getDiff(PCNT_UNIT_0, 0);
    pulse_diff_R[pulse_itr] = getDiff(PCNT_UNIT_1, 1);

    pulse_L[pulse_itr] += pulse_diff_L[pulse_itr];
    pulse_R[pulse_itr] += pulse_diff_R[pulse_itr];

    // 平均速度の計算
    int32_t L_ave = 0, R_ave = 0;

    for(byte i = 0; i < SPEED_BUFFER_LENGTH; i++) {
        byte itr_buff =  (pulse_itr + i) % SPEED_BUFFER_LENGTH;
        L_ave += pulse_diff_L[itr_buff] * SPEED_AVE_WEIGHT[i];
        R_ave += pulse_diff_R[itr_buff] * SPEED_AVE_WEIGHT[i];
    }
    L_ave /= SPEED_AVE_DIVISOR;
    R_ave /= SPEED_AVE_DIVISOR;
    
    crnt_pulse_per_sec_L = L_ave * 1000 / (int32_t)time_diff; 
    crnt_pulse_per_sec_R = R_ave * 1000 / (int32_t)time_diff; 


    // 速度制御
    // 誤差の計算
    error_L = tgt_pulse_per_sec_L - crnt_pulse_per_sec_L;
    error_R = tgt_pulse_per_sec_R - crnt_pulse_per_sec_R;

    integral_L += error_L * (int32_t)time_diff / DEFAULT_CONTROL_TIMESPAN;
    integral_R += error_R * (int32_t)time_diff / DEFAULT_CONTROL_TIMESPAN;

    if(integral_L >  INTEGRAL_LIMIT) integral_L =  INTEGRAL_LIMIT;
    if(integral_R >  INTEGRAL_LIMIT) integral_R =  INTEGRAL_LIMIT;
    if(integral_L < -INTEGRAL_LIMIT) integral_L = -INTEGRAL_LIMIT;
    if(integral_R < -INTEGRAL_LIMIT) integral_R = -INTEGRAL_LIMIT;
    

    // 目標速度が0 → 出力は強制で0にする
    if(tgt_pulse_per_sec_L == 0){
        out_L = 0;
    }else{
        out_L = (int32_t)
                (
                    Speed_Kp * error_L + 
                    Speed_Ki * integral_L +
                    Speed_Kd * (error_L - prev_error_L) / ((int32_t)time_diff / DEFAULT_CONTROL_TIMESPAN)
                ) * OUTPUT_SCALE_MULTIPLIER / OUTPUT_SCALE_DIVISOR;
        if(out_L > OUTTPUT_LIMIT_UPPER) {
            out_L = OUTTPUT_LIMIT_UPPER;
        } else if(out_L < OUTTPUT_LIMIT_LOWER) {
            out_L = OUTTPUT_LIMIT_LOWER;
        }
    }

    if(tgt_pulse_per_sec_R == 0){
        out_R = 0;
    }else{
        out_R = (int32_t)
                (
                    Speed_Kp * error_R + 
                    Speed_Ki * integral_R +
                    Speed_Kd * (error_R - prev_error_R) / ((int32_t)time_diff / DEFAULT_CONTROL_TIMESPAN)
                ) * OUTPUT_SCALE_MULTIPLIER / OUTPUT_SCALE_DIVISOR;
        
        if(out_R > OUTTPUT_LIMIT_UPPER) {
            out_R = OUTTPUT_LIMIT_UPPER;
        } else if(out_R < OUTTPUT_LIMIT_LOWER) {
            out_R = OUTTPUT_LIMIT_LOWER;
        }
    }

    // 誤差の更新
    prev_error_L = error_L;
    prev_error_R = error_R;

    // モータの出力
    if(out_L > 0){
        analogWrite(PIN_MOTOR_L_1, out_L);
        analogWrite(PIN_MOTOR_L_2, 0);
    }else{
        analogWrite(PIN_MOTOR_L_1, 0);
        analogWrite(PIN_MOTOR_L_2, -out_L);
    }

    if(out_R > 0){
        analogWrite(PIN_MOTOR_R_1, out_R);
        analogWrite(PIN_MOTOR_R_2, 0);
    }else{
        analogWrite(PIN_MOTOR_R_1, 0);
        analogWrite(PIN_MOTOR_R_2, -out_R);
    }


    portEXIT_CRITICAL_ISR(&speed_control_timer_mux);
    xSemaphoreGiveFromISR(speed_control_timer_semaphore, NULL);
}


// 通信周り
char serialBuff[64];
long nextPrint = 0;
#define PRINT_INTERVAL 200



void setup(){
    // シリアル通孫
    Serial.begin(115200);
    while (!Serial) {
        // シリアルポートが開くのを待つ
    }


    // エンコーダの設定
    pcnt_config_t pcnt_config;

    // encorder L

    // L-1 : channel 0 
    pcnt_config.pulse_gpio_num = PIN_MOTOR_L_ENC_A;
    pcnt_config.ctrl_gpio_num  = PIN_MOTOR_L_ENC_B;
    pcnt_config.lctrl_mode     = PCNT_MODE_REVERSE; // ctrl_gpioが lowの時のカウンタ増減
    pcnt_config.hctrl_mode     = PCNT_MODE_KEEP;    // ctrl_gpioがhighの時のカウンタ増減
    pcnt_config.pos_mode       = PCNT_COUNT_INC;    // 立ち上がりエッジの挙動
    pcnt_config.neg_mode       = PCNT_COUNT_DEC;    // 立ち下がりエッジの挙動
    pcnt_config.counter_h_lim  = COUNTER_MAX;       // カウンタの最大値
    pcnt_config.counter_l_lim  = COUNTER_MIN;       // カウンタの最小値
    pcnt_config.unit           = PCNT_UNIT_0;       //
    pcnt_config.channel        = PCNT_CHANNEL_0;    //
    pcnt_unit_config(&pcnt_config);//ユニット初期化

    //L-2 ;  channel 1
    pcnt_config.pulse_gpio_num = PIN_MOTOR_L_ENC_B;
    pcnt_config.ctrl_gpio_num  = PIN_MOTOR_L_ENC_A;
    pcnt_config.lctrl_mode     = PCNT_MODE_KEEP;    // ctrl_gpioが lowの時のカウンタ増減
    pcnt_config.hctrl_mode     = PCNT_MODE_REVERSE; // ctrl_gpioがhighの時のカウンタ増減
    pcnt_config.pos_mode       = PCNT_COUNT_INC;    // 立ち上がりエッジの挙動
    pcnt_config.neg_mode       = PCNT_COUNT_DEC;    // 立ち下がりエッジの挙動
    pcnt_config.counter_h_lim  = COUNTER_MAX;       // カウンタの最大値
    pcnt_config.counter_l_lim  = COUNTER_MIN;       // カウンタの最小値
    pcnt_config.unit           = PCNT_UNIT_0;       //
    pcnt_config.channel        = PCNT_CHANNEL_1;    //
    pcnt_unit_config(&pcnt_config);//ユニット初期化

    // encorder R

    // R-1 : channel 20
    pcnt_config.pulse_gpio_num = PIN_MOTOR_R_ENC_A;
    pcnt_config.ctrl_gpio_num  = PIN_MOTOR_R_ENC_B;
    pcnt_config.lctrl_mode     = PCNT_MODE_REVERSE; // ctrl_gpioが lowの時のカウンタ増減
    pcnt_config.hctrl_mode     = PCNT_MODE_KEEP;    // ctrl_gpioがhighの時のカウンタ増減
    pcnt_config.pos_mode       = PCNT_COUNT_INC;    // 立ち上がりエッジの挙動
    pcnt_config.neg_mode       = PCNT_COUNT_DEC;    // 立ち下がりエッジの挙動
    pcnt_config.counter_h_lim  = COUNTER_MAX;       // カウンタの最大値
    pcnt_config.counter_l_lim  = COUNTER_MIN;       // カウンタの最小値
    pcnt_config.unit           = PCNT_UNIT_1;       //
    pcnt_config.channel        = PCNT_CHANNEL_0;    //
    pcnt_unit_config(&pcnt_config);//ユニット初期化

    //R-2 ;  channel 1
    pcnt_config.pulse_gpio_num = PIN_MOTOR_R_ENC_B;
    pcnt_config.ctrl_gpio_num  = PIN_MOTOR_R_ENC_A;
    pcnt_config.lctrl_mode     = PCNT_MODE_KEEP;    // ctrl_gpioが lowの時のカウンタ増減;
    pcnt_config.hctrl_mode     = PCNT_MODE_REVERSE; // ctrl_gpioがhighの時のカウンタ増減;
    pcnt_config.pos_mode       = PCNT_COUNT_INC;    // 立ち上がりエッジの挙動;
    pcnt_config.neg_mode       = PCNT_COUNT_DEC;    // 立ち下がりエッジの挙動;
    pcnt_config.counter_h_lim  = COUNTER_MAX;       // カウンタの最大値;
    pcnt_config.counter_l_lim  = COUNTER_MIN;       // カウンタの最小値;
    pcnt_config.unit           = PCNT_UNIT_1;       //;
    pcnt_config.channel        = PCNT_CHANNEL_1;    //;
    pcnt_unit_config(&pcnt_config);//ユニット初期化;


    pcnt_counter_pause(PCNT_UNIT_0); //カウンタ一時停止;
    pcnt_counter_pause(PCNT_UNIT_1);
    pcnt_counter_clear(PCNT_UNIT_0); //カウンタ初期化;
    pcnt_counter_clear(PCNT_UNIT_1);
    Serial.begin(115200);
    pcnt_counter_resume(PCNT_UNIT_0);// カウント開始;
    pcnt_counter_resume(PCNT_UNIT_1);


    // タイマ割り込みのセットアップ;
    speed_control_timer_semaphore = xSemaphoreCreateBinary();
    speed_control_timer           = timerBegin(SPEED_CONTROL_TIMER_FREQ);

    timerAttachInterrupt(speed_control_timer  ,&speedTimerInterrupt  );
    timerAlarm(speed_control_timer  ,SPEED_CONTROL_TIMER_COUNT  ,true,0);

    //タイマ基準等間隔処理(print)の初期化
    nextPrint = millis() + PRINT_INTERVAL;

    tgt_pulse_per_sec_L = 2000;
    tgt_pulse_per_sec_R = 1000;
}


void loop(){
    if(nextPrint < millis()){{
        

        //  生値の表示
        // Serial.print(cnt_crnt[0]);
        // Serial.print(",");
        // Serial.print(cnt_crnt[1]);
        // Serial.print(",");
        // Serial.print(cnt_prv[0]);
        // Serial.print(",");
        // Serial.println(cnt_prv[1]);

        // 平均計算前のエンコーダ値と速度
        // Serial.print(pulse_L[pulse_itr]);
        // Serial.print(",");
        // Serial.print(pulse_R[pulse_itr]);
        // Serial.print(",");
        // Serial.print(pulse_diff_L[pulse_itr]);
        // Serial.print(",");
        // Serial.println(pulse_diff_R[pulse_itr]);


        // 平均計算後の速度
        Serial.print("ave p/s L : ");
        Serial.print(crnt_pulse_per_sec_L);
        Serial.print(",R");
        Serial.print(crnt_pulse_per_sec_R);
        Serial.println();

    
    }
        nextPrint = millis() + PRINT_INTERVAL;
    }
}

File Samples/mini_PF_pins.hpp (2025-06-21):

#ifndef MINI_PF_PINS_HPP
#define MINI_PF_PINS_HPP

// モータ出力
#define PIN_MOTOR_L_1 16
#define PIN_MOTOR_L_2 17
#define PIN_MOTOR_R_1 18
#define PIN_MOTOR_R_2 19

// モータエンコーダ
#define PIN_MOTOR_L_ENC_A 13
#define PIN_MOTOR_L_ENC_B 14
#define PIN_MOTOR_R_ENC_A 25
#define PIN_MOTOR_R_ENC_B 26

// PCとの通信(オプション)
#define PIN_PC_UART_RX 3
#define PIN_PC_UART_TX 1

// ラインセンサ
#define PIN_LINE_SENSOR_1 33
#define PIN_LINE_SENSOR_2 34
#define PIN_LINE_SENSOR_3 35

// LED
#define PIN_LED_RED 21
#define PIN_LED_YEL 22
#define PIN_LED_GRN 23

// 汎用IO
#define PIN_IO0 4
#define PIN_IO1 27
#define PIN_IO2 32
#define PIN_IO3 5

// 電源監視
#define PIN_VOLTAGE_MONITOR 36


#endif

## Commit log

2025-04-27 v0.1 基板のデータを追加
    [CPL-Moving_V4_ESP.csv, Moving_V4_ESP-CuBottom.gbr, Moving_V4_ESP-CuTop.gbr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]
2025-04-27 キャッシュファイルをトラッキングから削除
2025-04-27 gitignoreを追加
2025-04-27 版を追加
    [Moving_V4_ESP.kicad_sch]
2025-04-27 出力した回路図を追加
2025-04-27 readmeを追加
2025-04-27 フォルダ階層を変更
    [CPL-Moving_V4_ESP.csv, Moving_V4_ESP-CuBottom.gbr, Moving_V4_ESP-CuTop.gbr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]
2025-04-29 表の誤りを更新
2025-05-05 ピンアサインの定義ファイルを追加
2025-05-05 LED点灯のテストプログラムを追加
2025-05-05 モータのテストプログラムを追加
2025-05-05 シリアル通信のテストプログラムを作成
2025-05-05 フォトリフレクタのテストプログラムを追加
2025-05-05 ブラウザで表示するUIのテストプログラムを作成
2025-05-06 LittleFSのサンプルプログラムを追加
2025-05-06 ラジコン操作のベースプログラムを追加
2025-05-10 UART分圧抵抗にコンデンサを追加
    [Moving_V4_ESP.kicad_sch]
2025-05-10 フォトリフレクタのLED電流制限抵抗を50Ωに変更
    [Moving_V4_ESP.kicad_sch]
2025-05-10 フォトリフレクタをジャンパで選択できるように変更
    [Moving_V4_ESP.kicad_sch]
2025-05-18 機能ピンのプルアップ・プルダウンを追加
    [Moving_V4_ESP.kicad_sch]
2025-05-18 5Vの系列を追加
    [Moving_V4_ESP.kicad_sch]
2025-05-19 エンコーダ回路を追加(仮、要レベルコンバータ)
    [Moving_V4_ESP.kicad_sch]
2025-05-20 エンコーダ入力回路にレベルシフタを追加
    [Moving_V4_ESP.kicad_sch]
2025-05-20 汎用IOを追加。回路図はいったんシート外に記載。GPIO3にはDebug Logピンを使用
    [Moving_V4_ESP.kicad_sch]
2025-05-22 汎用IOのフットプリントを反映
    [Moving_V4_ESP.kicad_sch]
2025-05-22 エンコーダコネクタをZHに変更
    [Moving_V4_ESP.kicad_sch]
2025-05-22 入力専用ピンがGPIOに割り振られていたため、センサ入力ピンと交換
    [Moving_V4_ESP.kicad_sch]
2025-05-23 電源電圧監視回路を追加
    [Moving_V4_ESP.kicad_sch]
2025-05-23 不要な抵抗を削除
    [Moving_V4_ESP.kicad_sch]
2025-05-23 モータドライバの部品名を修正
    [Moving_V4_ESP.kicad_sch]
2025-05-26 回路図がシートに収まるようにレイアウト調整
    [Moving_V4_ESP.kicad_sch]
2025-05-26 電源コネクタを一つ削除
    [Moving_V4_ESP.kicad_sch]
2025-05-27 アノテーションを再実行
    [Moving_V4_ESP.kicad_sch]
2025-05-28 モード切替スイッチを削除
    [Moving_V4_ESP.kicad_sch]
2025-05-29 リセット用のジャンパー追加
    [Moving_V4_ESP.kicad_sch]
2025-05-29 電解コンデンサをDIP部品に変更
    [Moving_V4_ESP.kicad_sch]
2025-05-30 部品表に秋月の商品コードを追加
    [Moving_V4_ESP.kicad_sch]
2025-05-30 USB電源でモータを回すためのジャンパを追加
    [Moving_V4_ESP.kicad_sch]
2025-05-31 リセット用じジャンパをSMDスイッチが取り付けできる形に変更
    [Moving_V4_ESP.kicad_sch]
2025-06-01 ESP32のフットプリントを、背面パッドが裏面からはんだ付けできる形に変更
    [Moving_V4_ESP.kicad_sch]
2025-06-08 5VのDCDCコンバータを変更
    [Moving_V4_ESP.kicad_sch]
2025-06-08 回路図の版を更新
    [Moving_V4_ESP.kicad_sch]
2025-06-08 回路図を出力
2025-06-08 Revのテキストを更新
    [Moving_V4_ESP.kicad_pcb]
2025-06-08 主要部品をロック
    [Moving_V4_ESP.kicad_pcb]
2025-06-12 JP17のフットプリントをにDO41ダイオードが取付できる形に変更
    [Moving_V4_ESP.kicad_sch]
2025-06-14 誤ったジャンクションを削除
    [Moving_V4_ESP.kicad_sch]
2025-06-14 レイアウト都合での回路修正
    [Moving_V4_ESP.kicad_sch]
2025-06-14 部品を仮配置
    [Moving_V4_ESP.kicad_pcb]
2025-06-15 レイアウト都合でのピンアサイン変更
    [Moving_V4_ESP.kicad_sch]
2025-06-15 レイアウトを仮配線
    [Moving_V4_ESP.kicad_pcb]
2025-06-16 基本的なシルクを配置
    [Moving_V4_ESP.kicad_pcb]
2025-06-16 シルク・塗りつぶりを調整
    [Moving_V4_ESP.kicad_pcb]
2025-06-17 更新日を更新
    [Moving_V4_ESP.kicad_sch]
2025-06-17 回路図をエクスポート
2025-06-17 版を記入
    [Moving_V4_ESP.kicad_pcb]
2025-06-17 プロジェクトファイルを更新
2025-06-17 製造データを出力
    [bom.csv, designators.csv, positions.csv]
2025-06-19 readmeを更新
2025-06-19 EPS32S3をサポートから削除
2025-06-21 ピンアサインを最新のものに修正
2025-06-21 ピン定義ファイルを更新
2025-06-21 S3のピン設定ファイルのインクルードを削除
2025-06-29 3Dモデルを追加
2025-06-29 モータ制御のサンプルを追加(エンコーダ読み取りまで記述)
2025-07-06 モータ制御のサンプルに速度平均を算出する処理を追加
2025-07-06 モータ制御のサンプルに速度制御の処理を追加
